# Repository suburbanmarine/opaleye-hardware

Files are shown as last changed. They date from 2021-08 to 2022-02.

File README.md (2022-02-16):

# Opaleye Hardware

The Opaleye is the maritime smart node for maritime vision systems. Opaleye is a demonstration platform for underwater video acquisition and streaming. The intention is to form a basis for a "smart node" that can be used as part of a larger autonomous or remote-piloted robotic system.

The hardware is readily available and inexpensive.

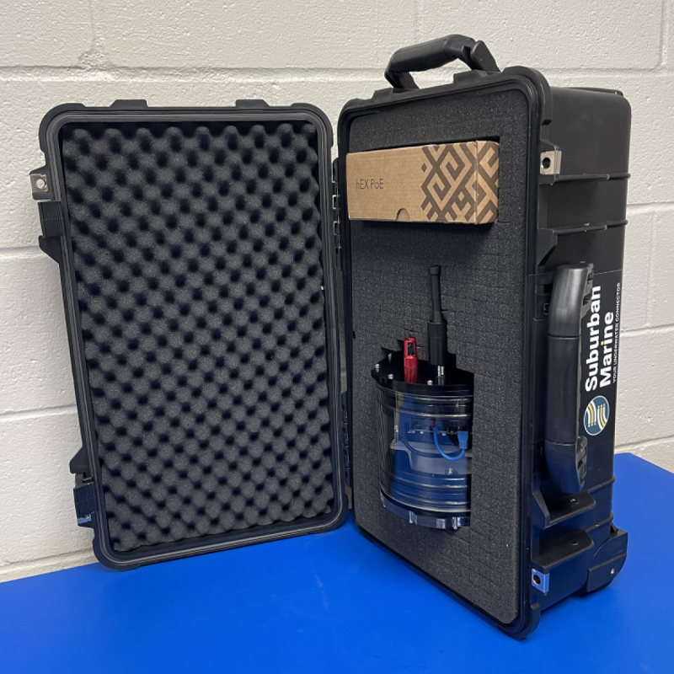
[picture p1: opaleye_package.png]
Opaleye package


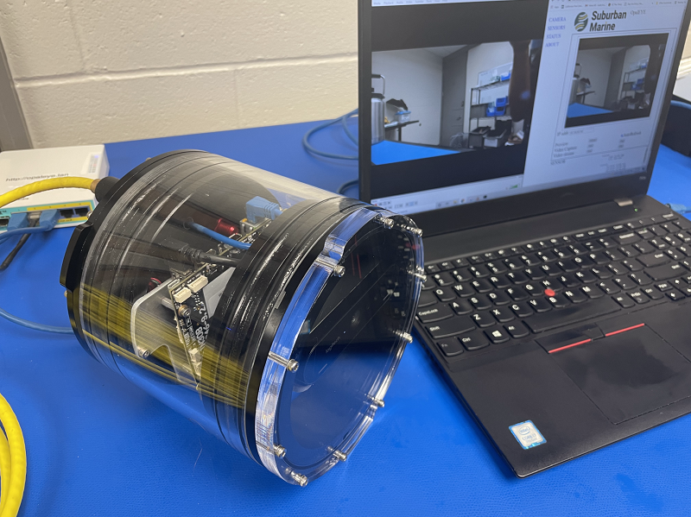
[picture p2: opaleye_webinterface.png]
Opaleye web interface


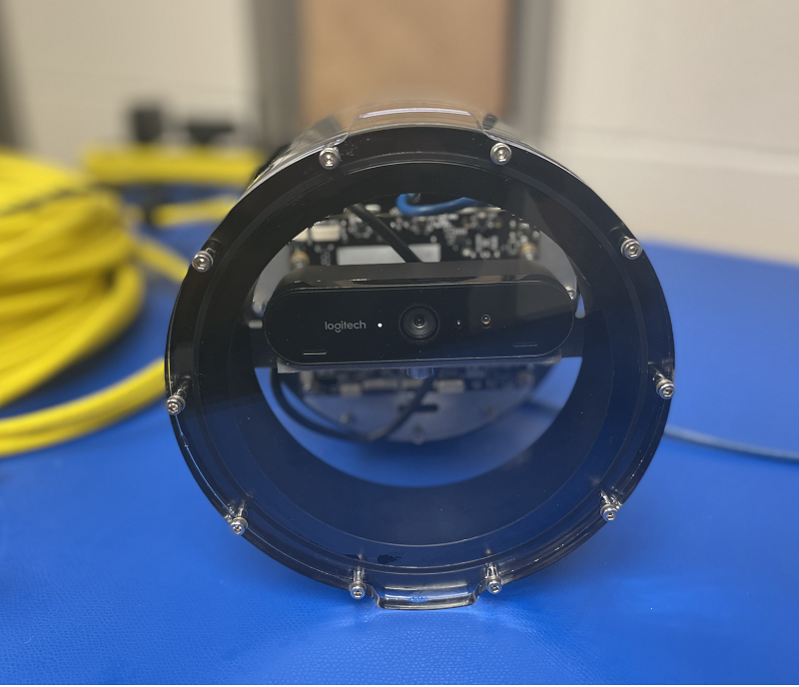
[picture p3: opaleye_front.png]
Opaleye front


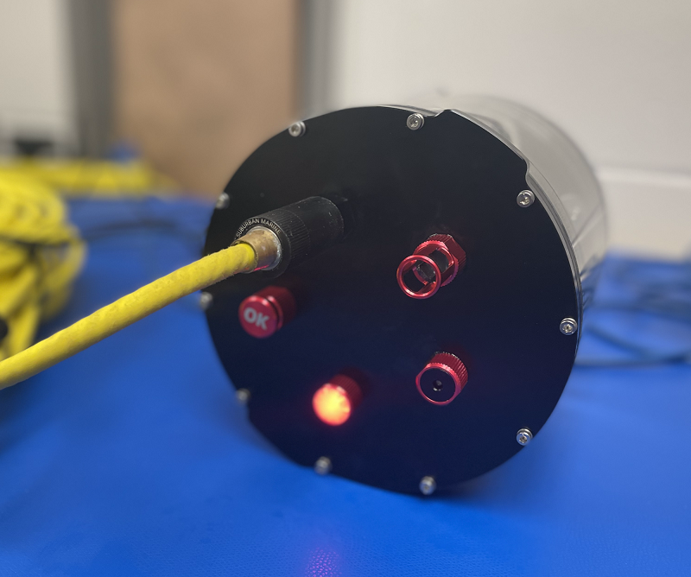
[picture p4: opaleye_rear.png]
Opaleye rear


## Block Diagram
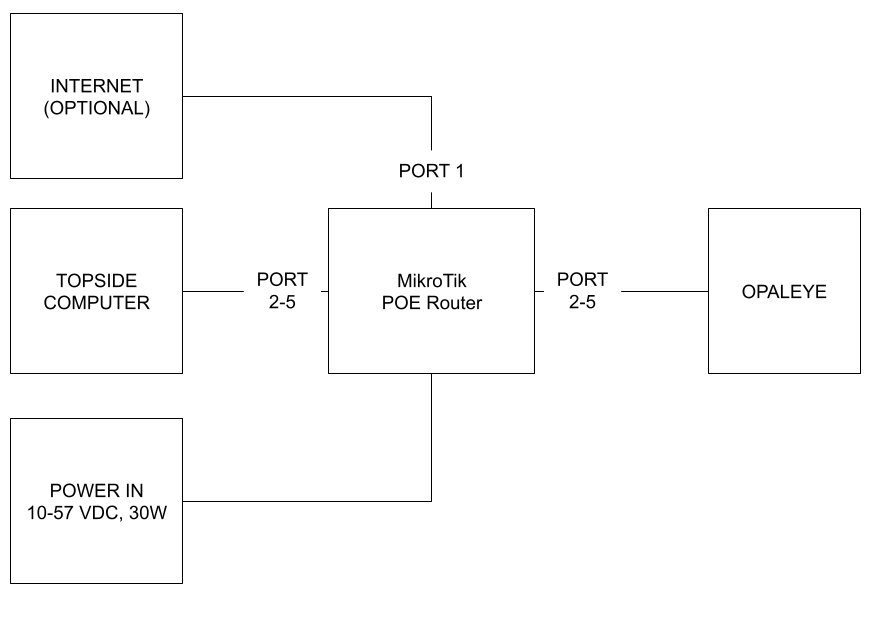
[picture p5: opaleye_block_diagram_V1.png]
Opaleye Block Diagram V1


## Features 

* Depth Rating: 200m
* Housing: Aluminum / Acrylic
* Port: Acrylic
* Operational Temperature: 0° C to 50° C

## BOM

Exploded view drawing: [SM-1610](/SM-1610_REV-A.PDF)

### Electronics
| Item | MFG | Part Number | Ea | Qty | Total |
| --- | --- | --- | --- | --- | --- |
| Camera | Logitech | BRIO | $145.95 | 1 | $145.95 |
| SOM | Nvidia | Nano | $130.00 | 1 | $130.00 |
| SBC Carrier | Auvidea | JN30B-PD | 206.21  | 1 | $206.21 |
| SOM Conduction Cool Plate | Connectech | XHG310 | $38.00  | 1 | $38.00  |
| RTC Battery | Seiko | MS621FE-FL11E | $3.00 | 1 | $3.00 |
| NVMe SSD | Samsung | MZ-V8V1T0B/AM | $119.99 | 1 | $119.99 |
| uSD Card | WD | SDSQQVR-064G-AN6IA | $28.21  | 1 | $28.21  |
| JST Connector | JST | \-- | $2.00 | 2 | $4.00 |
| Right Angle Ethernet Cable | Tripp-Lite | N201-SR1-BL | $4.04 | 1 | $4.04 |
| Right Angle USB A to RA USB C | BSHTU | B076DRR3VL | $7.99 | 1 | $7.99 |
| Temperature Sensor | Blue Robotics | CELSIUS-SENSOR-R1-RP | $60.00  | 1 | $60.00  |
| Pressure Sensor | Blue Robotics | BAR30-SENSOR-R1-RP | $72.00  | 1 | $72.00  |
| LED Indicator | Blue Robotics | INDICATOR-ASM-RED-R1-RP | $13.00  | 1 | $13.00  |
| | | | | Total | $832.39 |
### Hardware
| Item | MFG | Part Number | Ea | Qty | Total |
| --- | --- | --- | --- | --- | --- |
| Aluminum Endcap | Blue Robotics | WTE6-M-END-CAP-5-HOLE-R1-RP | $44.00 | 1 | $44.00  |
| O-ring Flange | Blue Robotics | WTE6-M-FLANGE-SEAL-R1-RP | $64.00 | 2 | $128.00 |
| Acrylic Endcap | Blue Robotics | WTE6-P-END-CAP-R1-RP | $42.00 | 1 | $42.00  |
| Acrylic Tube - Cut | ePlastics | Cut to length 6.5in OD tube x 5in length | $72.81 | 1 | $72.81  |
| SBC Heat Plate Mount | Waterjet West | SM-1606 | $50.00 | 1 | $50.00  |
| Logitech BRIO Mount | ForeCast 3D | SM-1611 | $50.00 | 1 | $50.00  |
| Baromax Male 8 Pin Connector | Suburban Marine  | BM-A-8-M | $75.00 | 1 | $75.00  |
| Baromax M10 Bulkhead | Suburban Marine  | BM-A-BH-B | $32.00 | 1 | $32.00  |
| Baromax Female 8 Pin Plug | Suburban Marine  | BM-A-8-F-D | $20.00 | 1 | $20.00  |
| Baromax Female Locking Ring | Suburban Marine  | BM-A-LR-F-A | $12.00 | 1 | $12.00  |
| M3 Hex Standoff x 14 mm Long, Brass | Würth Elektronik | 970140324 | $0.67  | 4 | $2.68 |
| 1/4"-20 x 1/4" SCHS | McMaster Carr | 92196A533 | $0.25  | 1 | $0.25 |
| M3 x .05 x 6mm SHCS | McMaster Carr | 91292A111 | $0.11  | 13 | $1.44 |
| M3 x .05 x 8mm SHCS | McMaster Carr | 91292a112 | $0.05  | 7 | $0.36 |
| M3 x .05 x 16mm SHCS | McMaster Carr | 91292A115 | $0.07  | 10 | $0.68 |
| M3 x .05 x 12mm 316SS SCHS | McMaster Carr | 92290A117 | $0.26  | 10 | $2.59 |
| Silica Gel Dessicant Bag | McMaster Carr | 2189K16 | $0.70  | 1 | $0.70 |
| | | | | Total | $534.52 |

### Tether
| Item | MFG | Part Number | Ea | Qty | Total |
| --- | --- | --- | --- | --- | --- |
| Tether Cable Option 1 | Molex | CABLE ETHERNET5E 4X2X#24, 1554316010, per meter | $9.90  | 0 | $0.00 |
| Tether Cable Option 2 | Blue Robotics | CAB-NBPUF-4UTP-26AWG, per meter | $5.00  | 0 | $0.00 |
| Baromax Female 8 Pin Connector | Suburban Marine | BM-A-8-F | $75.00 | 1 | $75.00  |
| Baromax Inline Backshell | Suburban Marine | BM-A-IL-B | $32.00 | 1 | $32.00  |
| Baromax Female Locking Ring | Suburban Marine | BM-A-LR-F-A | $12.00 | 1 | $12.00  |
| | | | | Total | $119.00 |

### Topside Hardware
| Item | MFG | Part Number | Ea | Qty | Total |
| --- | --- | --- | --- | --- | --- |
| PoE Router | Mikrotik | RB960PGS | $79.00 | 1 | $79.00  |
| PWR Supply | MeanWell | SGA60U48-P1J| $31.65 | 1 | $31.65  |
| | | | | Subtotal | $110.65 |

## License

The Opaleye Hardware Design is released under the Creative Commons Attribution-ShareAlike 4.0 International (CC BY-SA 4.0) license. Full license details are availible in the LICENSE.txt file.

These files are copyright 2021 Suburban Marine, Inc.

## Revision History

1.0 - Initial Release

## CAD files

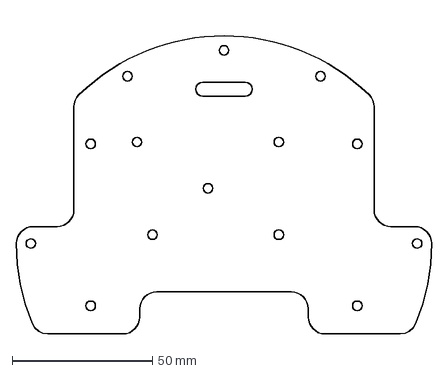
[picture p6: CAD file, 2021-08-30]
SM-1606_REV-B.DXF
148.0 x 113.2 mm

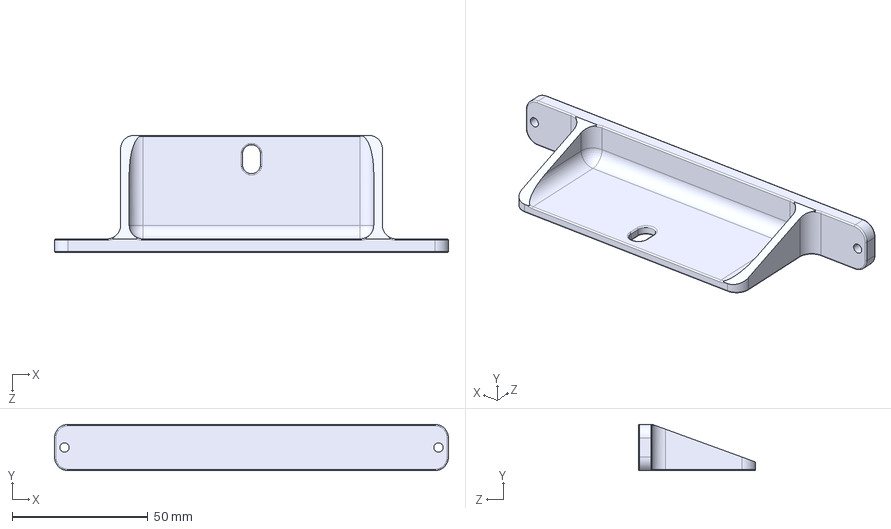
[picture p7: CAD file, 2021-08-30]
SM-1611_Rev-A.STEP
145.0 x 17.1 x 43.2 mm

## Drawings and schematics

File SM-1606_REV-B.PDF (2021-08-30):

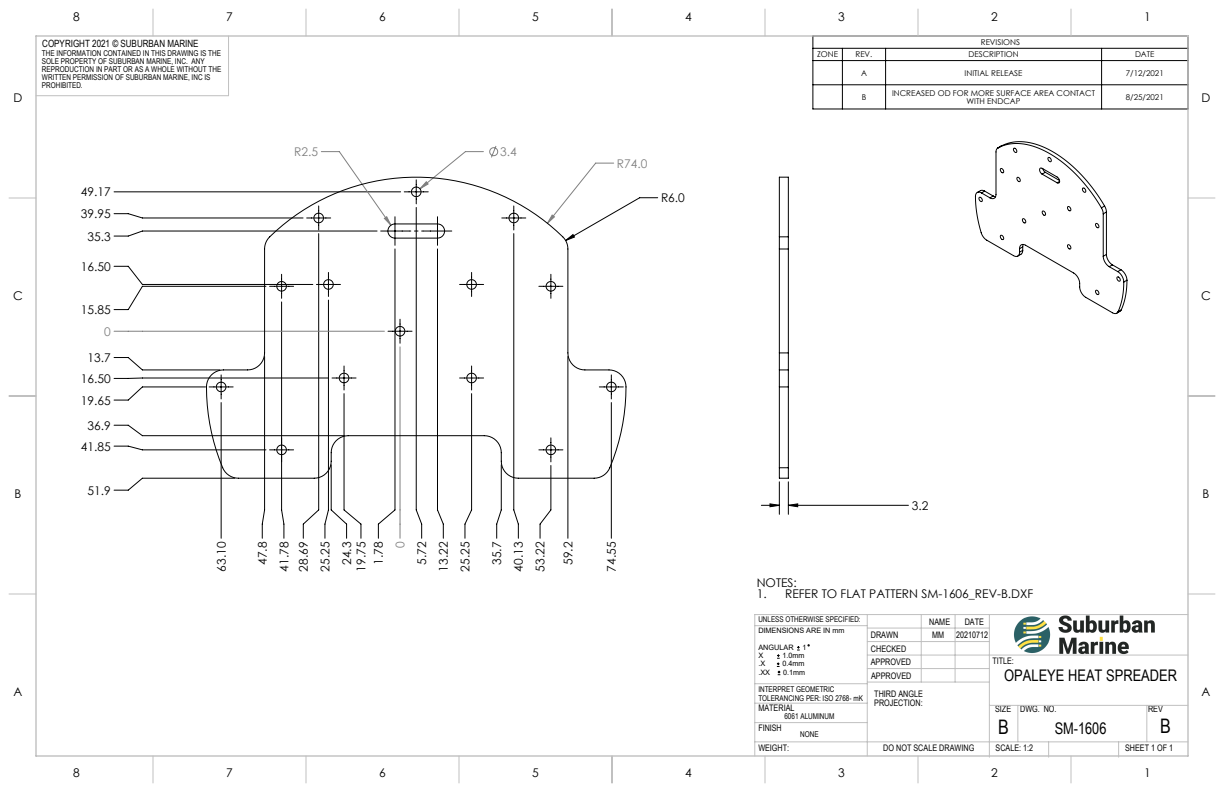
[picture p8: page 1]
DO NOT SCALE DRAWING; SHEET 1 OF 1; SCALE: 1:2

COPYRIGHT 2021 © SUBURBAN MARINE THE INFORMATION CONTAINED IN THIS DRAWING IS THE SOLE PROPERTY OF SUBURBAN MARINE, INC. ANY REPRODUCTION IN PART OR AS A WHOLE WITHOUT THE WRITTEN PERMISSION OF SUBURBAN MARINE, INC IS PROHIBITED. | | REVISIONS

ZONE | REV. | DESCRIPTION | DATE

A | INITIAL RELEASE | 7/12/2021
B | INCREASED OD FOR MORE SURFACE AREA CONTACT WITH ENDCAP | 8/25/2021

NOTES:
1. REFER TO FLAT PATTERN SM-1606_REV-B.DXF

UNLESS OTHERWISE SPECIFIED: | | NAME | DATE
DIMENSIONS ARE IN mm ANGULAR 1 X 1.0mm .X 0.4mm .XX 0.1mm | DRAWN | MM | 20210712

CHECKED
APPROVED | | | TITLE: OPALEYE HEAT SPREADER
APPROVED

INTERPRET GEOMETRIC TOLERANCING PER: ISO 2768- mK | THIRD ANGLE PROJECTION:
MATERIAL 6061 ALUMINUM | | SIZE B | DWG. NO. SM-1606 | REV B

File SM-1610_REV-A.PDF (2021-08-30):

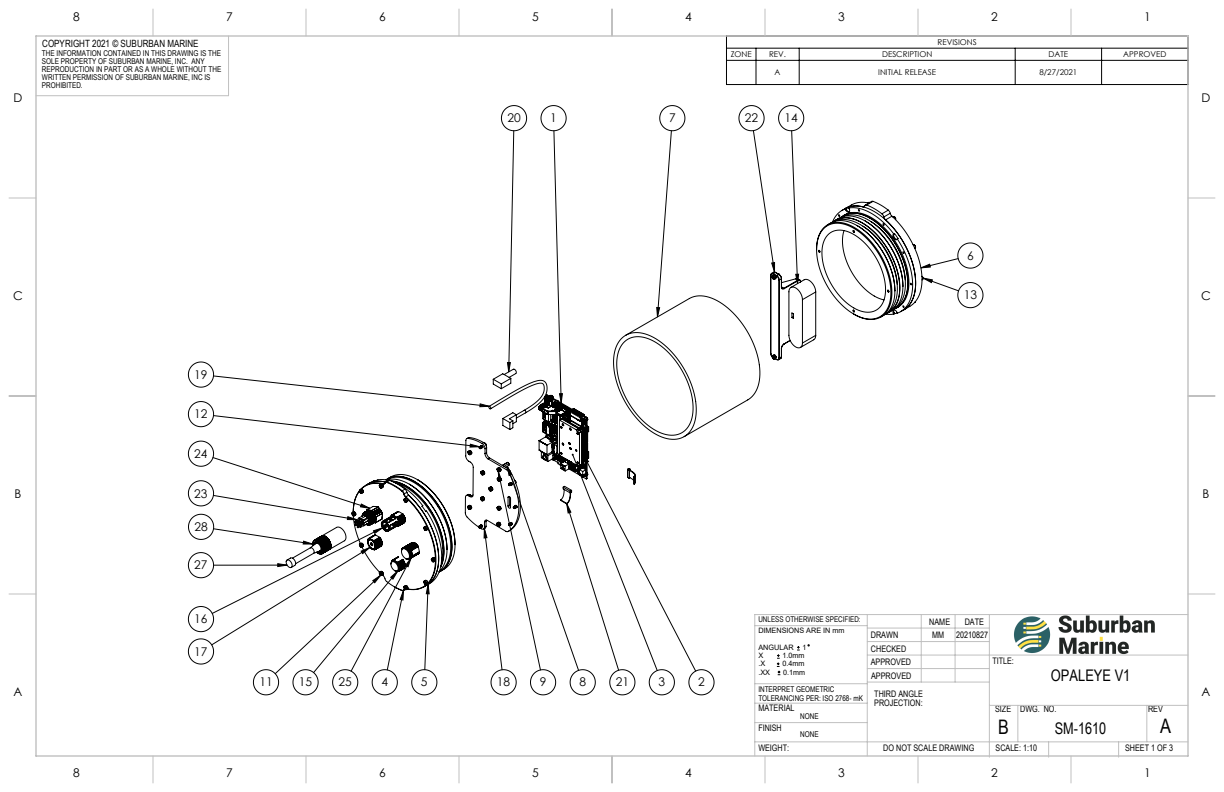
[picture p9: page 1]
DO NOT SCALE DRAWING; SHEET 1 OF 3; SCALE: 1:10

COPYRIGHT 2021 © SUBURBAN MARINE THE INFORMATION CONTAINED IN THIS DRAWING IS THE SOLE PROPERTY OF SUBURBAN MARINE, INC. ANY REPRODUCTION IN PART OR AS A WHOLE WITHOUT THE WRITTEN PERMISSION OF SUBURBAN MARINE, INC IS PROHIBITED. | | REVISIONS

ZONE | REV. | DESCRIPTION | DATE | APPROVED

A | INITIAL RELEASE | 8/27/2021

UNLESS OTHERWISE SPECIFIED: | | NAME | DATE
DIMENSIONS ARE IN mm ANGULAR 1 X 1.0mm .X 0.4mm .XX 0.1mm | DRAWN | MM | 20210827

CHECKED
APPROVED | | | TITLE: OPALEYE V1
APPROVED

INTERPRET GEOMETRIC TOLERANCING PER: ISO 2768- mK | THIRD ANGLE PROJECTION:
MATERIAL NONE | | SIZE B | DWG. NO. SM-1610 | REV A

ITEM
NO. | PART NUMBER | DESCRIPTION | QTY.
30 | 9452K419 | OIL-RESISTANT BUNA-N O-RING, 1/4 FRACTIONAL WIDTH, DASH NUMBER 432 | 4
29 | 9452K181 | OIL-RESISTANT BUNA-N O-RING, 3/32 FRACTIONAL WIDTH, DASH NUMBER 162 | 2
28 | BM-A-LR-F-A | BAROMAX LOCKING RING, SIZE A, FEMALE | 1
27 | BM-A-8-F-D | BAROMAX FEMALE 8 PIN PLUG | 1
26 | BM-A-N-C-C | NUT, SIZE A, BLUE ROBOTICS M10 THREAD, 6061 AL | 1
25 | VENT-ASM-R3-RP | ENCLOSURE VENT AND PLUG | 1
24 | BM-A-BH-B | BAROMAX BULKHEAD BACKSHELL M10 | 1
23 | BM-A-8-M | BAROMAX CONNECTOR MALE 8-PIN | 1
22 | SM-1611 | BRIO MOUNT BRACKET | 1
21 | SM-1609 | JST CONNECTOR J22 | 2
20 | B076DRR3VL | RIGHT ANGLE USB A TO RA USB C | 1
19 | SM-1607 | RIGHT ANGLE 8P8C CONNECTOR | 1
18 | SM-1606 | OPALEYE HEAT SPREADER | 1
17 | BAR30-SENSOR-ASSEMBLY-R1 | | 1
16 | CELSIUS-TEMPERATURE-SENSOR-ASSEMBLY-X1 | | 1
15 | INDICATOR10-ASM-R1 | | 1
14 | LOGITECH_BRIO_CAMERA | | 1
13 | 91292A115 | 18-8 STAINLESS STEEL SOCKET HEAD SCREW, M3 X 0.5 mm THREAD, 16 mm LONG | 10
12 | 91292A112 | 18-8 STAINLESS STEEL SOCKET HEAD SCREW, M3 X 0.5 mm THREAD, 8 mm LONG | 7
11 | 92290A117 | Super-Corrosion-Resistant 316 Stainless Steel Socket Head Screw, M3 x 0.5 mm Thread, 12 mm Long | 10
10 | 92196A533 | 18-8 Stainless Steel Socket Head Screw, 1/4"-20 Thread Size, 1/4" Long | 1
9 | 91292A111 | 18-8 STAINLESS STEEL SOCKET HEAD SCREW, M3 X 0.5 mm THREAD, 6 mm LONG | 13
8 | 95947A511 | M3 X 14mm BRASS HEX STANDOFF | 4
7 | SM-1612 | WTE6 BLUE ROBOTICS TUBE CUT LENGTH | 1 | UNLESS OTHERWISE SPECIFIED: | | NAME | DATE
| | | | DIMENSIONS ARE IN mm ANGULAR 1 X 1.0mm .X 0.4mm .XX 0.1mm | DRAWN | MM | 20210827
| | | | | CHECKED
| | | | | APPROVED | | | TITLE: OPALEYE V1
| | | | | APPROVED
3 | XHG310 | | 1 | INTERPRET GEOMETRIC TOLERANCING PER: ISO 2768- mK | THIRD ANGLE PROJECTION:
2 | NVIDIA_NANO_MODULE_P3448 | NOT SPECIFIED | 1
6 | WTE6-P-END-CAP-R1 | 1
5 | WTE6-M-FLANGE-SEAL-R1 | 2
4 | WTE6-M-END-CAP-5-HOLE-R1 | 1
1 | AUVIDEA_JN30B-PD_70788_38346 | 1 | NONE
A
DWG. NO. | REV
B

SIZE

MATERIAL

A | A
B | B
C | C
D | D

SM-1610

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

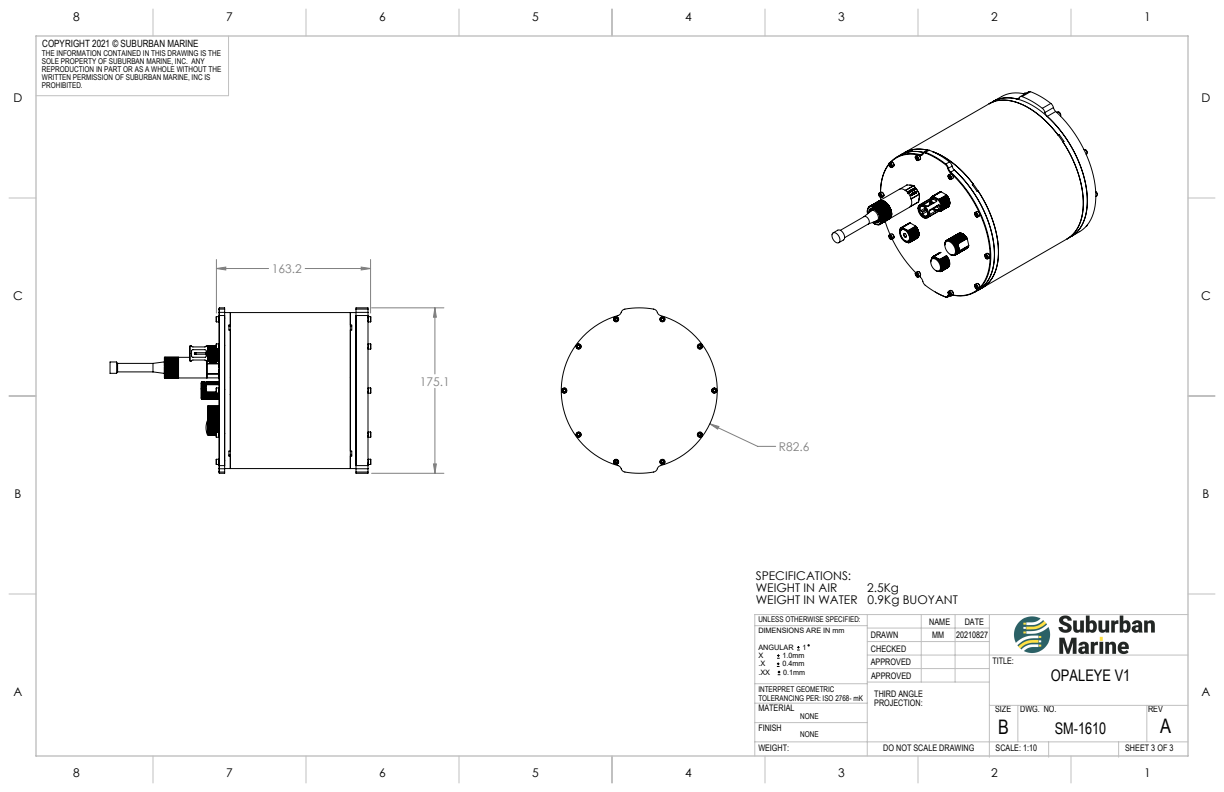
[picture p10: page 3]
WEIGHT IN AIR

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

SPECIFICATIONS:
WEIGHT IN WATER 0.9Kg BUOYANT

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

CHECKED
APPROVED | | | TITLE: OPALEYE V1
APPROVED

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

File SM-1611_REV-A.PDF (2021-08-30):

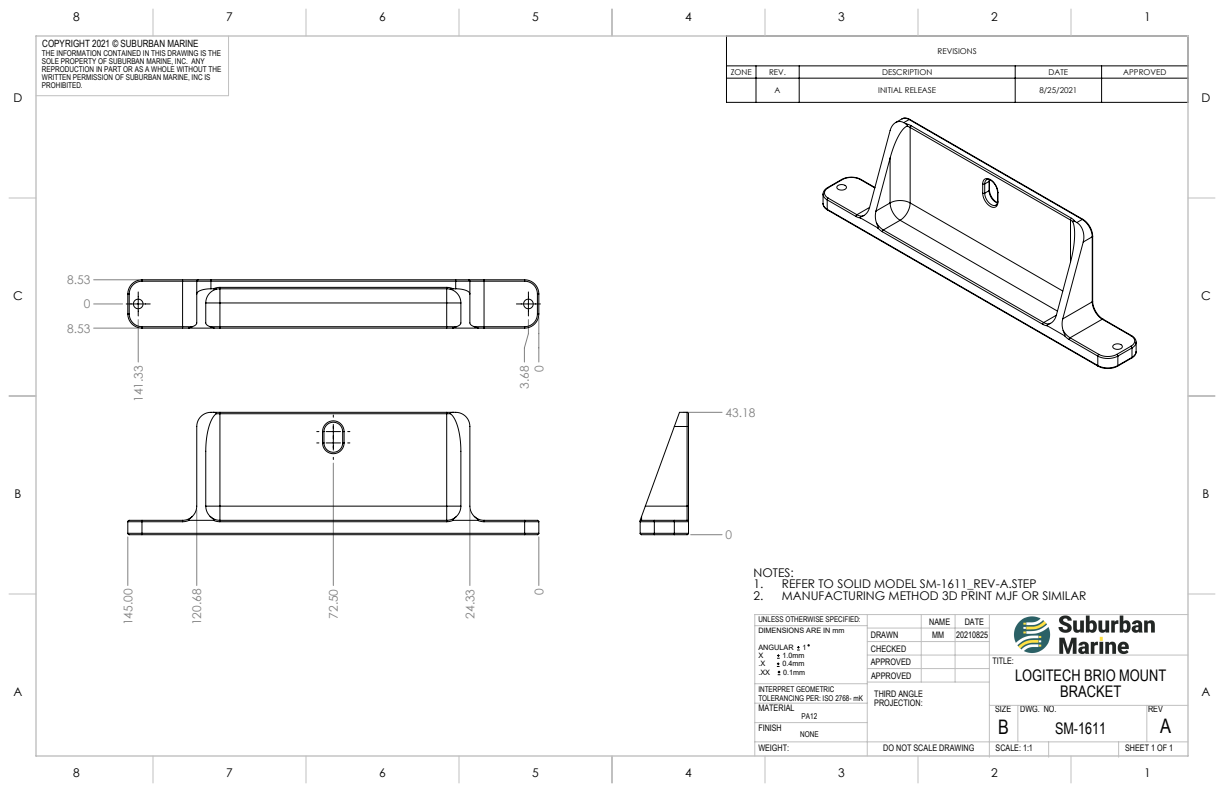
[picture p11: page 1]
DO NOT SCALE DRAWING; SHEET 1 OF 1; SCALE: 1:1

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

ZONE | REV. | DESCRIPTION | DATE | APPROVED

A | INITIAL RELEASE | 8/25/2021

NOTES:
1. REFER TO SOLID MODEL SM-1611_REV-A.STEP
2. MANUFACTURING METHOD 3D PRINT MJF OR SIMILAR

UNLESS OTHERWISE SPECIFIED: | | NAME | DATE
DIMENSIONS ARE IN mm ANGULAR 1 X 1.0mm .X 0.4mm .XX 0.1mm | DRAWN | MM | 20210825

CHECKED
APPROVED | | | TITLE: LOGITECH BRIO MOUNT BRACKET
APPROVED

INTERPRET GEOMETRIC TOLERANCING PER: ISO 2768- mK | THIRD ANGLE PROJECTION:
MATERIAL PA12 | | SIZE B | DWG. NO. SM-1611 | REV A
